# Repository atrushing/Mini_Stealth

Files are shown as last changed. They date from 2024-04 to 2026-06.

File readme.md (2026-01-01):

## Mini Stealth - A Scaled Down Stealthburner

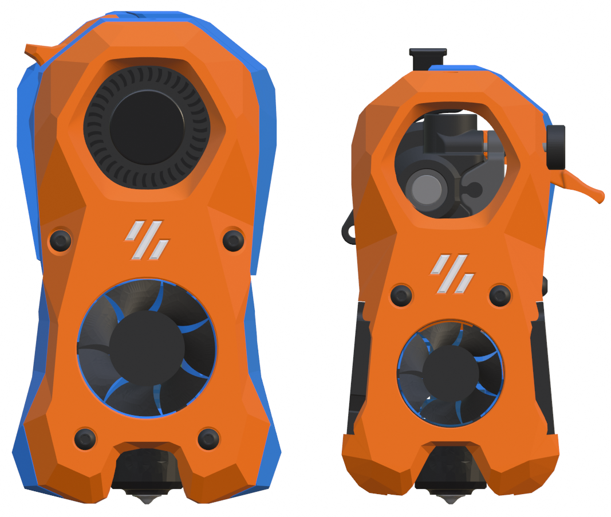
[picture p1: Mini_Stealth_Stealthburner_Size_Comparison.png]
Size Comparison


This is the Version 2 release of the Mini Stealth toolhead. It is about 5/8 the size of the official Stealthburner and weighs considerably less. It uses a pair of 4010 blowers for part cooling and a 3010/2510 fan for the hotend. The blowers use glued in [air guides](https://www.teamfdm.com/forums/topic/1886-vorpal-180-a-printed-printer/?do=findComment&comment=13431&_rid=1756) to increase airflow by [about 20%](https://www.teamfdm.com/forums/topic/1886-vorpal-180-a-printed-printer/?do=findComment&comment=13566&_rid=1756) compared to the Mini Stealth v1. This toolhead was entirely designed in Blender Blender and I only have mesh files available.

The new design mounts the extruder and hotend to a *[core piece](https://www.teamfdm.com/forums/topic/1886-vorpal-180-a-printed-printer/?do=findComment&comment=15428&_rid=1756)* and mounts the blowers, hotend fan and LEDs into the *shroud* that slides onto the core. This makes assembly and maintenance much easier and the extruder can be fully removed while the core remains installed on the printer. There are thirteen extruders supported by the Mini Stealth.

| Orbiter 1.5 | Orbiter 2.0 | Sherpa Mini | LGX Lite | VzHextrudort |
| --- | --- | --- | --- | --- |
| WristWatch BMG | WristWatch G2SA | Sherpa Micro¹ | HGX Lite | Galileo2 SA  |
| Hummingbird | ProtoXtruder <small>(v1&v2)</small> | Creality K1 | | |

¹ <small>There is also a mirrored version of the Sherpa Micro that adds a filament release lever on the left side</small>

There are currently 24 different hotends supported by this toolhead. The cores for the top four in the chart are shared by the others in each group. The bottom ten hotends each have their own cores.

| Slice Mosquito | Phaetus Rapido | Phaetus Dragon ST/HF | T-Labs Dragon ACE |
|:---:|:---:|:---:|:---:|
| Mellow NF Crazy Volcano | Phaetus Rapido UHF | DropEffect neXtG | Goliath |
| Nitram VolcoMosq | Phaetus Dragon UHF | Triangle Labs TZ V6  | |
| | Triangle Labs T-Vocano Dragon | | |
| | Triangle Labs CHCB-V V6DM | | |
| | DropEffect neXtG UHF | | |
| | | | |
| Phaetus Dragonfly BMO | Revo Voron | Bambu Lab X1 |  Creality K1 |
| Phaetus Dragonfly BMS7  | E3D V6 compatible² | Creality Spider Pro  | |
| Phaetus Dragonfly BMS6  | Triangle Labs TCHC TD6S | Dropeffect XG | |

² <small>E3D V6 compatible hotends fit into UHF shrouds and require a clamp secured with 2x M3x10 screws.</small>

Here is an example of how the core and shroud are assembled. There are pockets for 3x6mm magnets. If the magnets aren't seated completly flush, they can prevent the shroud from seating in the correct location.

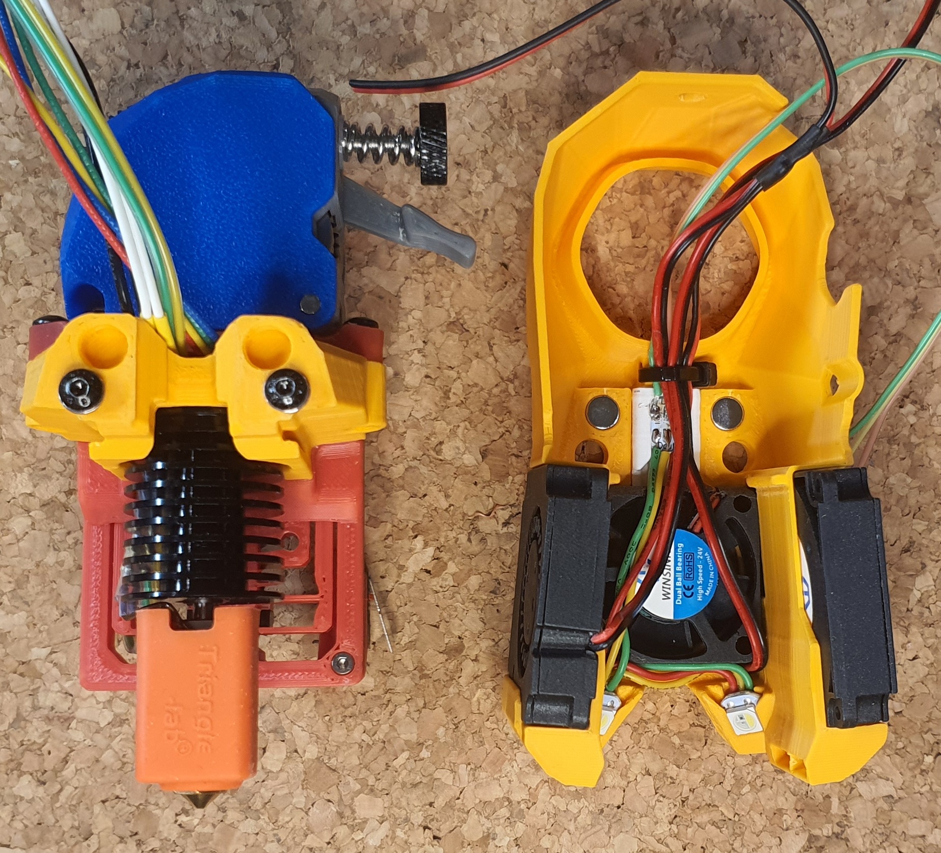
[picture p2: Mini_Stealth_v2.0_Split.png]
Mini Stealth Split


Looking closely you can see three M3 shim washers (DIN988) stacked under each of the M3x40 BHC screws securing the core to the [DAB x-carriage](https://www.teamfdm.com/files/file/760-mini-stealth-dab-beta-release/). Some component combinations will require these shims, such as with the MGN9 mod on a V0.1/2 in order to avoid crushing the linear carriage when installing. It is best practice to do a dry-run and measure clearances before final installation.

The .stl files in the Common_Parts folder should be compatible across the entire range of Mini Stealth versions. This includes all of the x-carriage options (DAB as well) and supplemental parts such as LED mounts and diffuser.

There are 90 different shrouds grouped by extruder type. Each of the 90 shrouds comes in four flavors. The basic shroud, a ZeroClick version and left or right probe-mount versions. The last two use M2.5x6 flathead screws to fit brackets that hold [six different probes](https://raw.githubusercontent.com/atrushing/Mini_Stealth/main/Ender_3_parts/Ender_3_Probe_Options_1.png). There are also versions of all of these shrouds designed to fit a 2510 hotend fan. The Goliath shrouds are only available as CropTop with a 2510 fan. 

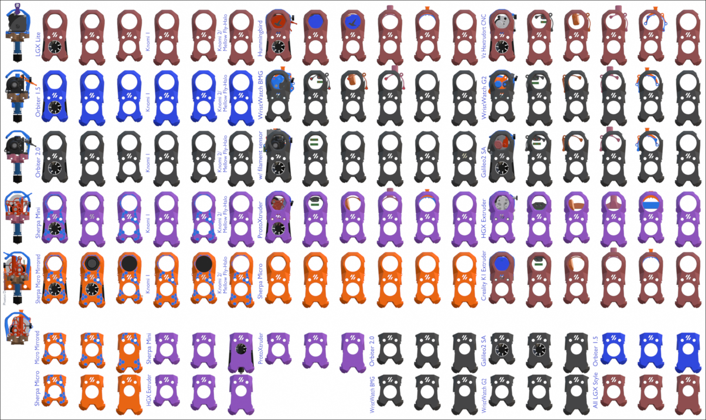
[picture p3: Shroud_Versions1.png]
Shroud Versions1


There are six sets of core pieces with unique mounting holes for different extruder groups. Each extruder folder has a copy of the applicable core pieces to avoid confusion. The extruders in the image above with magenta shrouds all use an adapter plate to secure the extruder to the core piece. 

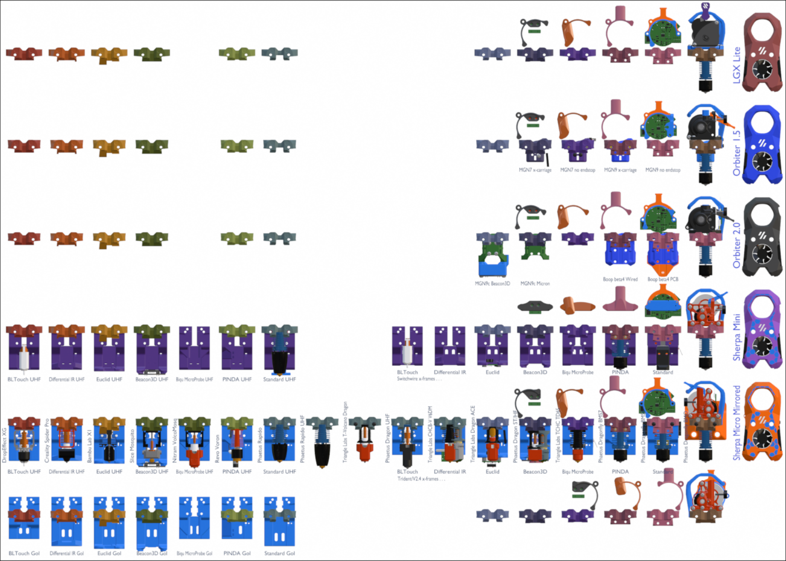
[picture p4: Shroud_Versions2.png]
Shroud Versions2


There are four different motor bridge pieces for each extruder that address different cable management options. The umbilical PCB option uses a pair of heat-set inserts to secure a secondary printed piece. The motor_bridge for the cable chains uses M2.5 flathead screws threaded into the plastic to attach the secondary piece.

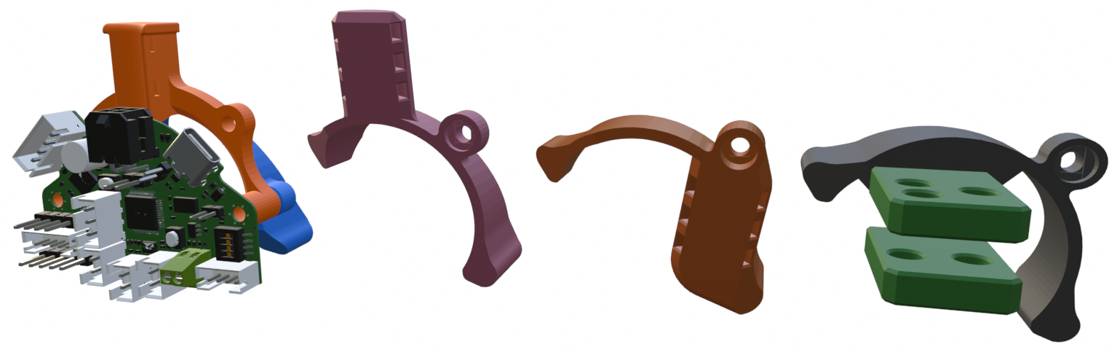
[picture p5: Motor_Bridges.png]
Motor Bridges


### Heatset Inserts

- The only hotends that require heat-set inserts are the Bambu and the Dragonfly BMS models.

- Most of the extruders are secured with two inserts from below the *core* piece but some use M3 square nuts installed from the side of the *core*

- Most of the x-carriages will use a pair of inserts from the back to secure the *core*

- Most of the cable_doors will use one insert on the non-hinged side to secure it to the back side of the *core*

- A few cable_doors use two inserts on either side at the bottom and then hook under the top of the shroud

- The Omron probe (and Klicky) requires a pair of inserts in the retainer_bracket behind the x-frames

- Mounting a Beacon/Cartographer probe uses two inserts in the bottom of the x-frames

- The motor_bridge mounts for 2 or 3 hole cable chains will require inserts

- Mounting an umbilical PCB requires two inserts. Depending on which 
  extruder is used, the second image below shows where they are installed

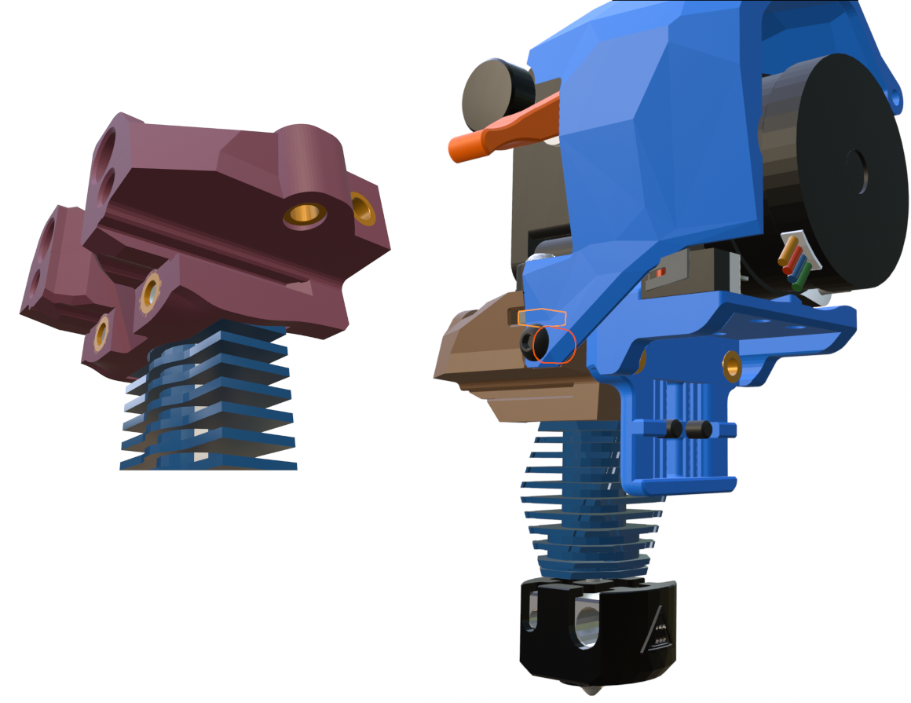
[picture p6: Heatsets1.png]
Heatsets1


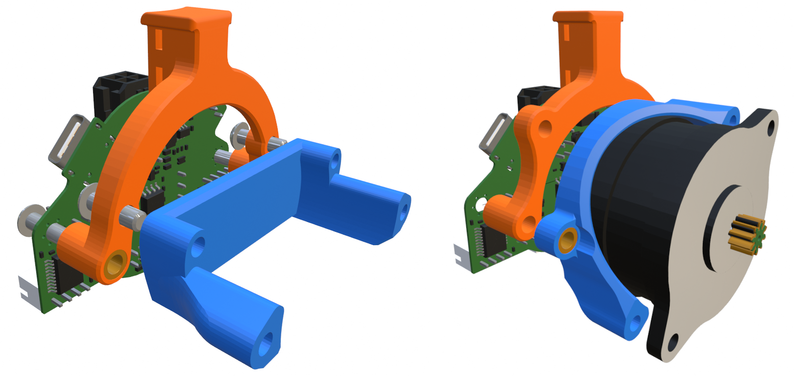
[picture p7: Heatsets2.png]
Heatsets2


### Mini Stealth - Vz Goliath Hotend Versions

This is an effort at making a shroud to fit the Goliath Air hotend. There are only crop-top shrouds available which use 4010 blowers for part cooling and a 2510 radial fan for cooling the hotend heat-break.

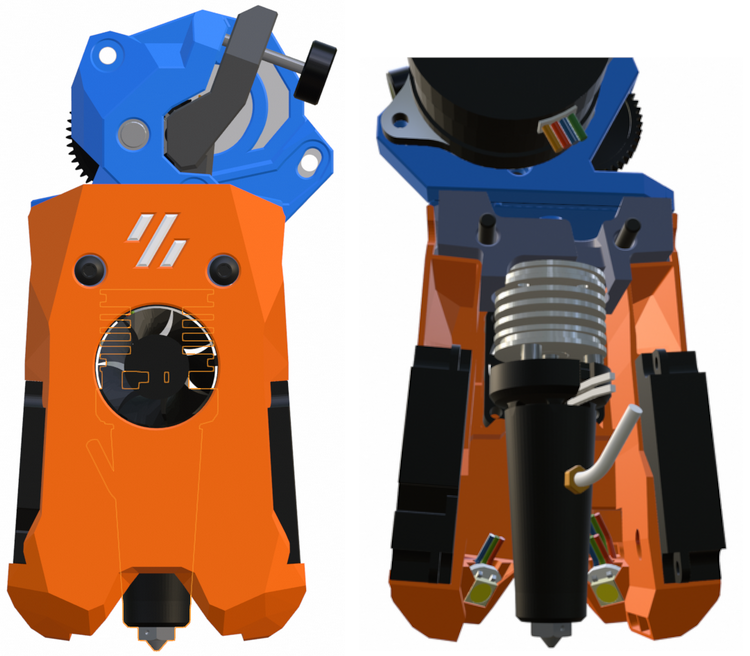
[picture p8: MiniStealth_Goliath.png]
Goliath 01


The Goliath hotend fits onto any of the existing DragonAce core pieces in this repository. As installed, the nozzle sits 18.5mm lower than any of the standard length hotends and 10mm lower than the UHF hotends.

There are spring clips built into the shroud to hold the 2510 fan in place. They are designed with a 0.3mm gap that will not require supports but should allow them to act as springs. These might still need some adjustment.

### Addendum

I still need to work up new assembly instructions for this v2 toolhead. For supporting these designs, I am most active over on [TeamFDM.com](https://www.teamfdm.com/profile/1756-atrushing/content/?type=downloads_file&change_section=1) and will be happy to [answer questions](https://www.teamfdm.com/forums/topic/3433-mini-stealth-v2-is-available) there. The Mini Stealth files available on TeamFDM are of the version 1 release, while the current v2 files are all here.

I started working on a [configurator](https://atrushing.github.io/Sidewinder-Switchwire/) for this toolhead but I still have a lot to learn about JavaScript. If anyone would like to help with this, please drop me a message on [TeamFDM](https://www.teamfdm.com/profile/1756-atrushing/).

If you would like to support the development of these mods I would be very grateful. [](https://paypal.me/atrushing)

### - - Changelog - -

#### 20 Dec 2025

- Added WristWatch Orbiter 2.x extruder and Mini Stealth shrouds for it

#### 19 Dec 2025

- Minor geometry improvement for WW-BMG shrouds

#### 16 Nov 2025 

- Added WW BMG remix with Filament Cutter

#### 26 Oct 2025 

- Added x-carriage to fit the Tiny-M printer

#### 25 Sep 2025 

- Added BTT Eddy side-mount variants

#### 3 Sep 2025 

- Added x-frames for Voron Legacy printers

#### 31 May 2025 

- Merge pull request #6 from darkautism/main
- Add 4040 VSlot support

#### 22 May 2025

- Added new cores for E3D V6 compatible hotends (to fit UHF shrouds)

#### 14 May 2025

- Added rigid x-carriages for MGN12C and MGN12H linear rails

#### 1 May 2025

- Added rigid x-carriages for MGN9C and MGN9H linear rails

#### 24 Apr 2025

- Updated DAB design and readme instructions

#### 6 Apr 2025

- Added StealthChanger backplate and dock in the Common Parts folder

#### 30 Mar 2025

- Modified new core pieces to allow JST connector to fit through wire channel
- Added new style of core pieces for all extruders supported by Mini Stealth

#### 26 Mar 2025

- Added Prusa MK3 x-carriage options

#### 16 Mar 2025

- Added new style of core pieces for the Sherpa Mini mount extruders

#### 6 Feb 2025

- Added support for WristWatch BMG & G2SA extruders

- There are now two versions for the Sherpa Micro, normal and mirrored. (the mirrored version fits my modification with a filament release lever on the left side)

- Added the modded+mirrored Sherpa Micro .stl files in this repo

- Added support for HGX Lite extruder

- Added support for Creality K1 extruder

- Added support for Goliath hotend (CropTop only)

- Added 2.4/Trident x-frames for Goliath hotend

- Minor shroud geometry cleanup

- Fixed mis-aligned first layer of x-frame pieces

- Added support for 2510 hotend fan to all shroud options

- Added right side probe support

- Added new hex patterns to fit the 2510 shrouds

- Re-organized GitHub folder structure based on extruder selection

- Update and improve readme files

#### 6 Apr 2024 v2.0 Release

- More extruders have been added.

- More hotends have been added.

- The shroud is now separate from the core.

- The shroud fits onto the core with a pair of sliding grooves and can fit magnets to improve the connection as needed.

- The hotend can be installed to the core and then mounted to the printers' gantry.

- Everything else can be installed (or removed) while on the printer.

- All core pieces and shrouds are compatible with 25mm or 26mm x-carriages. :: i.e. Mini Stealthburner CNC aluminum carriages.

- All x-carriages are compatible with any hotend/extruder combination.

- There are specific UHF x-frames for Trident, V2.4 and Switchwire printers to provide probe compatibility.

- The V0.1/V0.2 x-carriages are much stiffer with side ribs that require included XY_Joint_Upper pieces.

- The 25mm spacing improves the Ender 3 mount which is available in the repo.

- The LED diffuser and carriage are new and simplified.

- The Rainbow BARF carriage is now in two part and should be easier to fit.

- All shrouds have standard, ZeroClick and Differential IR options.

- The 4010 blowers use a glued in (CA glue) air guide to increase airflow at the nozzle.

- The UHF shrouds have been re-worked to put the 4010 blowers lower, matching the standard shrouds.

- New probe mounting side brackets have been added that fit the Differential IR shrouds. Thanks to @Titus A Duxass for the concept!
  
  - Biqu MicroProbe
  
  - PINDA
  
  - BL-Touch

- I have added Knomi2 shrouds that should also fit the Mellow Fly-Halo display.

- I have made Crop-Top shrouds for each extruder option.

- Each extruder has motor_bridge pieces that support cable management, cable chain mounts or umbilical PCB mounting.

- The umbilical PCB mounts are vertical for better ADXL readings.

- All parts have been modified for cleaner and more consistent geometry across versions.

#### 16 May 2023 v1.2.5

- Added Euclid and Biqu MicroProbe mounts for Trident, 2.4 and Switchwire

- Upload corrected version of ZeroClick Mount

#### 12 Apr 2023 v1.2.5

- Added missing Crop-Top .stl and image

#### 4 Mar 2023 v1.2.5

- Added feature to x-frame_right to allow mounting X limit switch as with the Umbilical Mod

- Added Beacon3D compatible x-frame sets for V2.4, Trident and for Switchwire

- Added new shrouds to fit the Creality Spider Pro hotend

#### 28 Feb 2023 v1.2.4

- Added wire slot for LEDs wires to fit past 3010 fan. The last revision wasn't sufficient.

- All shroud files are new.

#### 26 Feb 2023 v1.2.3

- Fixed pinching of LED wires when using 3010 fan.

#### 24 Feb 2023 v1.2.2

- Improved rigidity of x-carriage mounting for the V0.1/V0.2 by moving the heat-set insert to the back side.

- This requires 5mm longer screws to mount the shroud.

- Improved how the front two screws fit into the shroud when mounting onto the carriage. This used to be chamfered but now is flat for better load transfer. All shroud .stl files are new.

- Uploaded new version of x-frame pieces with more clearance to fit 4010 blowers from different suppliers.

- Added x-frame pieces for Switchwire builds. These pieces can fit the standard capacitive probe or fit a BL-Touch. Since the stepper sits very low with the Orbiter, the Z height of the nozzle is raised by 3mm compared to the official Switchwire x-frame design.

#### 22 Feb 2023 v1.2.1

- Added a hex pattern and tutorial based on the 3DP-MAMSIH mod

#### 13 Feb 2023 v1.2.0

- Improved cooling by aiming ducts 6 deg lower at hotend nozzle tip.

- Added compatibility with 3010 hotend fan. 3007 fan still fits using clip-in adapter

- Added versions for ZeroClick mod

- Added versions for differential IR probe.

- Added newer version for the VolcoMosq hotend

- Minor geometry cleanup.

- All shroud .stl files are new

#### 10 Feb 2023

- Release of Sherpa Mini version

#### 31 Jan 2023 v1.1.7

- Added stretched versions for the Rapido UHF, Dragon UHF and the VolcoMosq hotends

#### 19 Jan 2023 v1.1.6

- Added Umbilical-mod mount remixed from skuep's mod

- Replaced motor_bridge with version with space for M3 heat set inserts to allow for mounting PCB or Umbilical-mod behind the stepper

#### 22 Nov 2022 v1.1.5

- Added versions for Slice Mosquito hotend

#### 10 Nov 2022 v1.1.4

- Added an x_carriage for the V0.1 MGN-9 mod

#### 1 Nov 2022

- Release of LGX Lite version

#### 24 Oct 2022 v1.1.3

- Added versions to fit the Rapido HF hotend

#### 22 Oct 2022 v1.1.2

- Added versions to fit the Revo Voron hotend

#### 22 Oct 2022 v1.1.1

- Fixed mesh error in [a]_MIni_Stlb_Orbiter_2.0_main_body.stl

#### 17 Oct 2022 v1.1.0

- Fixed wire clearance issue on x_carriage_mini_stlb

- Updated all main_body files with with more room for cable routing

#### 15 Oct 2022 v1.0.1

- Added versions for compatibility with the Dragon hotend

- Changed naming scheme for better description of versions

#### 14 Oct 2022 v1.0.0

- Modified 'cable_door' due to interference with V0.1 x-axis endstop.

#### 13 Oct 2022

- Release of Orbiter 2.0 version

#### 30 Sept 2022

- Initial Mini Stealth release (Orbiter 1.5 version)

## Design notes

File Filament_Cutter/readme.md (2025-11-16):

### Wrist Watch BMG with Side Mounted Filament Cutter

This is a remix of the [WW BMG](https://github.com/bythorsthunder/Voron_Mods/tree/main/Wristwatch_Extruder_BMG) extruder which adds a filament cutter below the hobbed gears. It fits replacement Bambu blades and uses a spring from a clicker pen (5mm x 20mm) to keep the blade clear of the filament path until actuated.

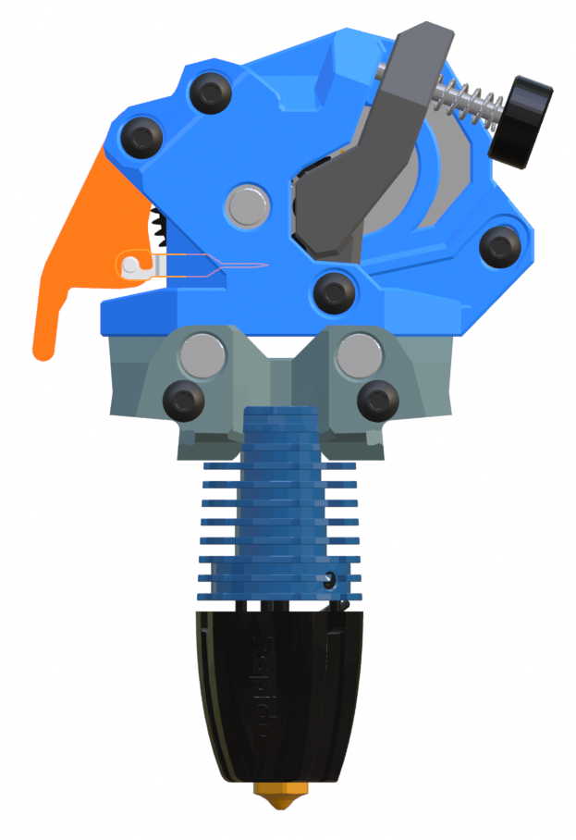
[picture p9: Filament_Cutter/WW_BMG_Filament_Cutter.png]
WW BMG FC


This remix doesn't change any of the functional geometry of the extruder. The cutter arm does require organic supports for the small hook feature that helps grabbing the blade. It uses up to an M3x20 screw for the pivot of the cutter arm. The blade recess in the extruder body might need a little cleanup to ensure that the blade can slide smoothly.

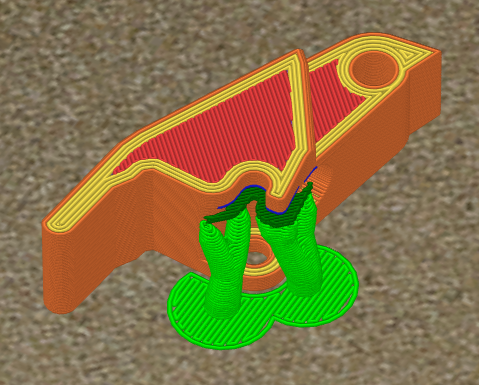
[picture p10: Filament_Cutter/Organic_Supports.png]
Tree Supports


There is an additional subtraction part that removes the necessary material from the Mini Stealth shroud to allow the cutter arm to fit. It has two locating cylinders to align the .stl with the shroud in the slicer. It is easiest to align the parts from the bottom view.

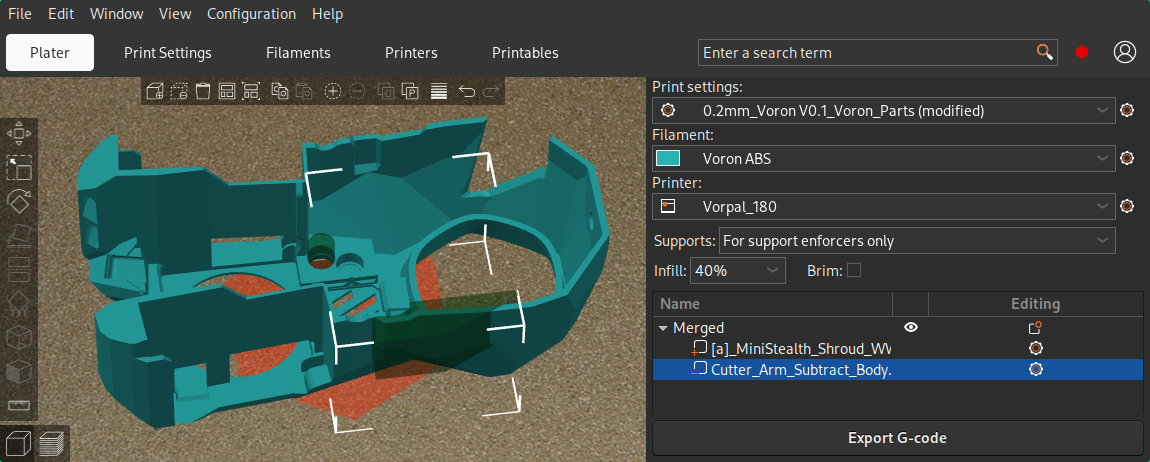
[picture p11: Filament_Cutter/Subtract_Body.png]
Subtract Body


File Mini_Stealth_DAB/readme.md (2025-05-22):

## Mini Stealth DAB

This is a flexure based nozzle probing option for mounting the Mini Stealth toolhead in a Voron Trident or V2.4. It uses a simple linear compliant mechanism to provide ~0.5mm of Z travel while being quite rigid in the other axes. It weighs around 20g fully assembled with Z and X endstops. It should require the same Print_Start preparations as the Voron TAP to ensure a clean nozzle and accurate probing. While probing with a scale on top of the bed, it applys about 600g of force.

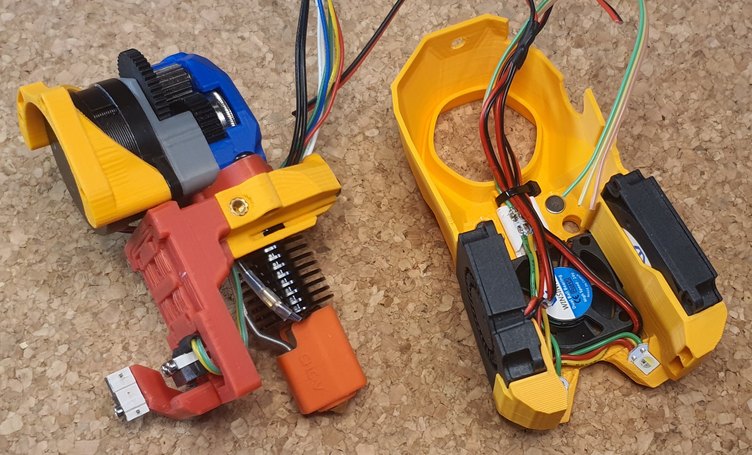
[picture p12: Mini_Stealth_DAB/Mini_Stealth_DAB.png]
Mini Stealth DAB


The new version of the DAB has been adapted to work with my new rigid core pieces. This combination is more reliable than before. While probing, the old version would flex back before lifting the toolhead. It now creates a box structure centered on the linear carriage which restrains the movement better along the Z axis.

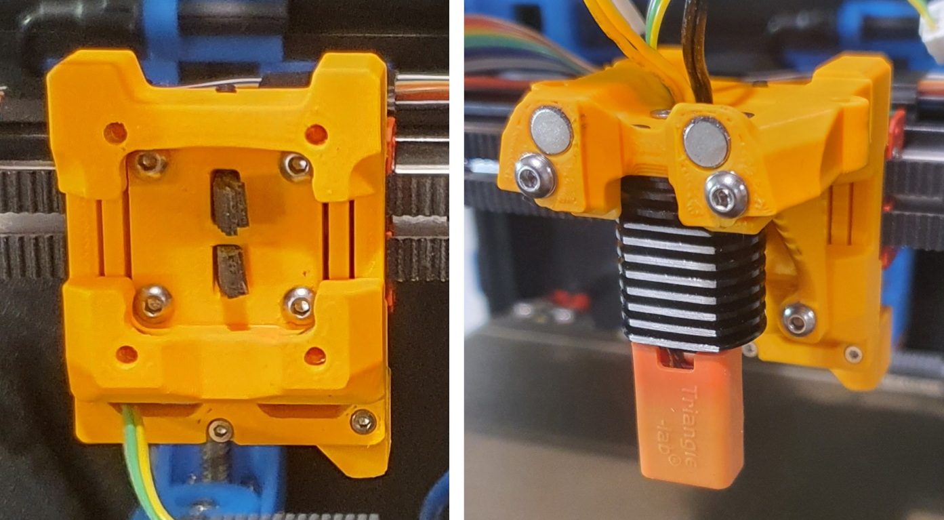
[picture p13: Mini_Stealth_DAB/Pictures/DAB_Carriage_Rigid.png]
Rigid DAB


There are a few supports (shown in green) built in to make printing more reliable. After printing, the two inner sections will need to be gently, but firmly, pried apart from the two bridge sections while being careful not to plastically deform the flexures. There are four pockets for M3 square nuts to secure the Mini Stealth core piece using two M3x45 BHCS at the top and two M3x12 BHCS on the bottom.

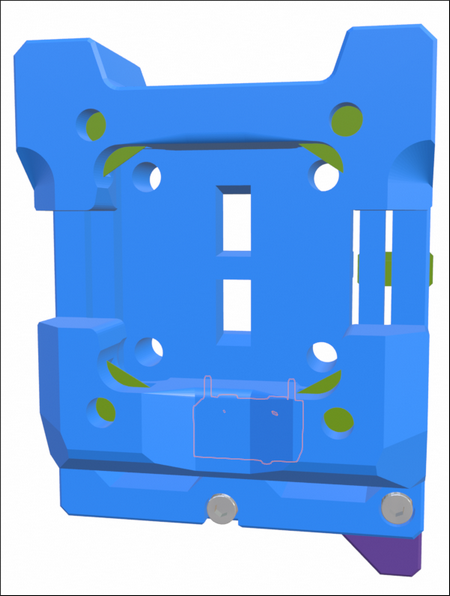
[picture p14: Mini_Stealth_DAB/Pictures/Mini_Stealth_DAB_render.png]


There are several different rear boss pieces depending on where you have your X endstop mounted. This piece is secured with a pair of M2x10 self tapping screws.

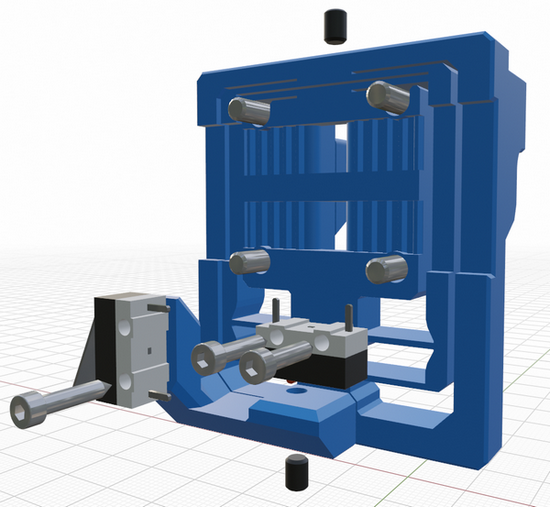
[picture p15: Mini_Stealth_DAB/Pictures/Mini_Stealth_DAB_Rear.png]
Rear View


The flexure works as shown below. The blue center section is fixed to the MGN12H linear carriage. The magenta vertical bars are the intermediate phase and the purple outside frame is the final phase of the flexure. The red bars are the actual flexing parts and are 0.8mm thick.

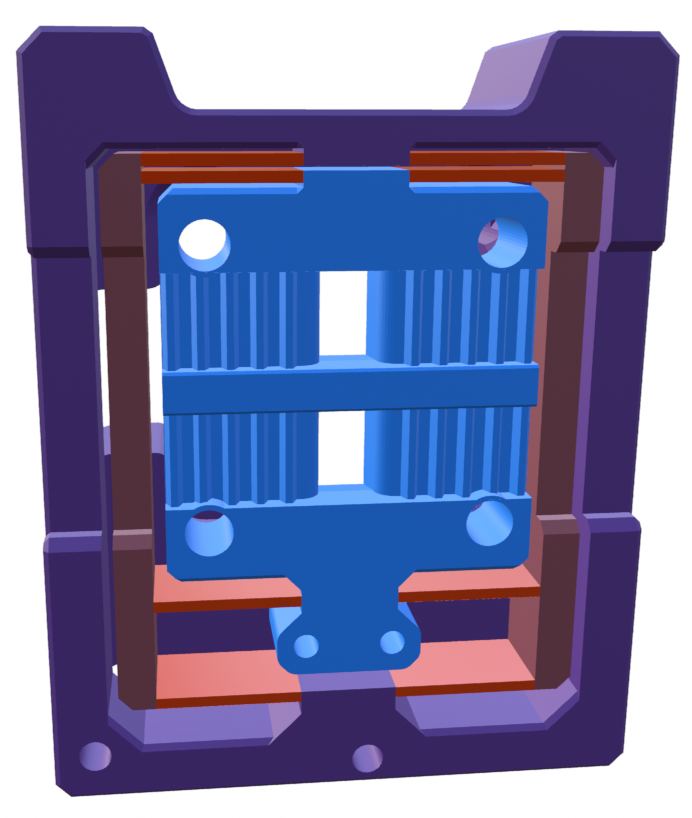
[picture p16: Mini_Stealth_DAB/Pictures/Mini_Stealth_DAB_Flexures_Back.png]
Flexure


### Assembly

- After ensuring that the flexure moves freely, install one of the grub 
  screws in the top and screw it in just enough to remove the reverse Z travel in
   the flexure. This provides a known lower limit of travel.

- Install the Z_Stop_Boss with two M2 x 10 screws from the front.

- Install the Z micro-switch with the red trigger on the left 
  (viewed from the back). The wires can be fed to the front through the 
  lower gap in the flexure.

- Install the other M3 grub screw on the bottom of the DAB_Z_Boss. Screw
   it in until you hear the micro-switch trigger, then slowly turn it back out
   until the trigger releases. This makes the trigger travel distance less
   than 0.5mm.

- Mount the x-carriage to the MGN12C carriage with four M3x12 BHCS. 
  There is room to pull the four belt ends through and trim them at the 
  front face of the DAB.

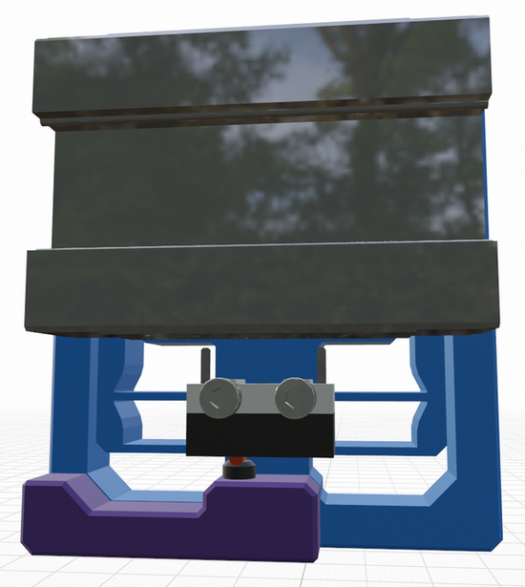
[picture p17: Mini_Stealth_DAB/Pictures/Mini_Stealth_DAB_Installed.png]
DAB Assembled


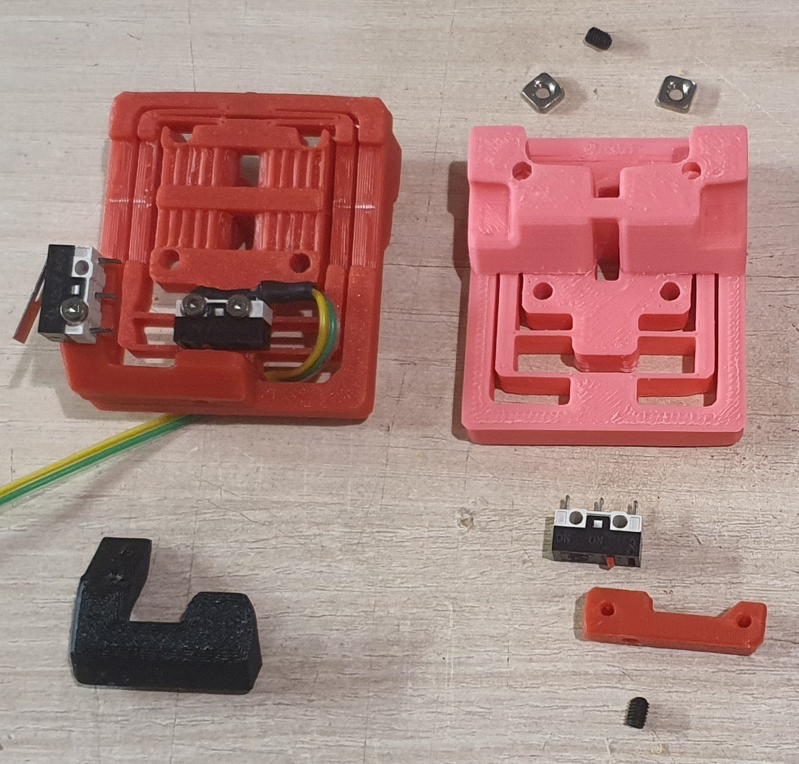
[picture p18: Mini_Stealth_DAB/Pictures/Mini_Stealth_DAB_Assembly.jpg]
Assembled DAB


### Stealthburner Version

This version of DAB is a drop-in replacement for the Stealthburner x-frame pieces. It uses slightly different hardware than the official Stealthburner assembly, as shown in the picture below.

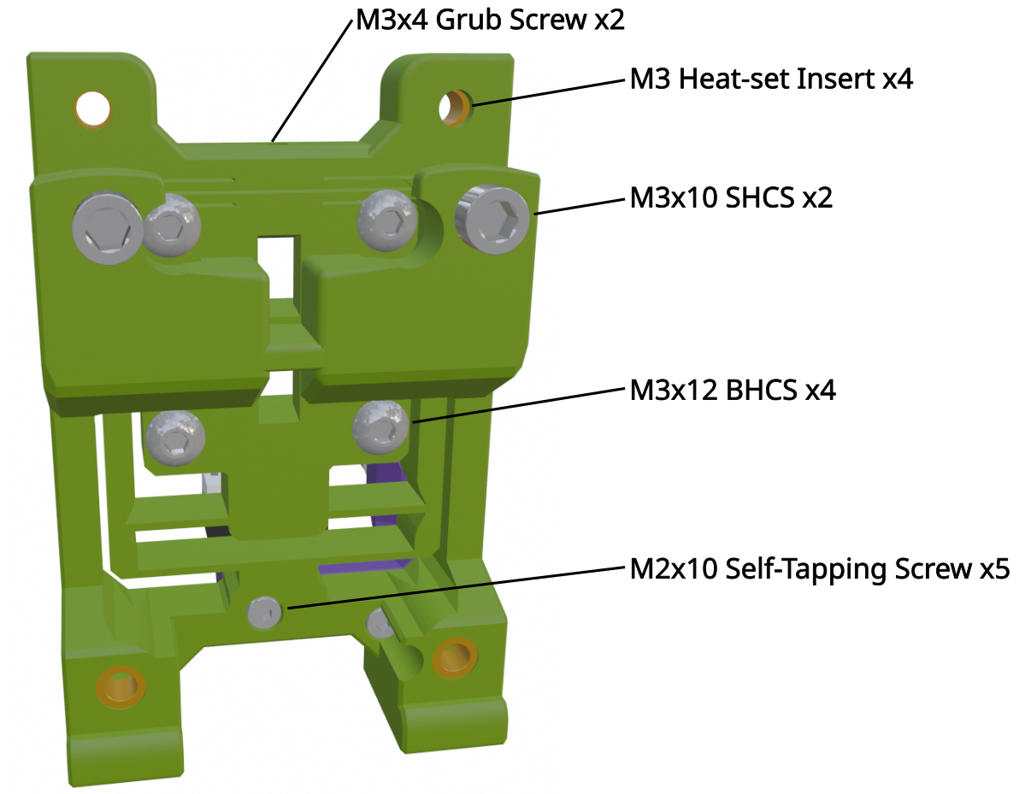
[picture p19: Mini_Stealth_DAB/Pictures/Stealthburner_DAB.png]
Stealthburner DAB


### Stealthburner on a Switchwire

This version of DAB fits a Stealthburner onto a Switchwire. It is printed in two parts and assembled with three M2x10 self tapping screws.

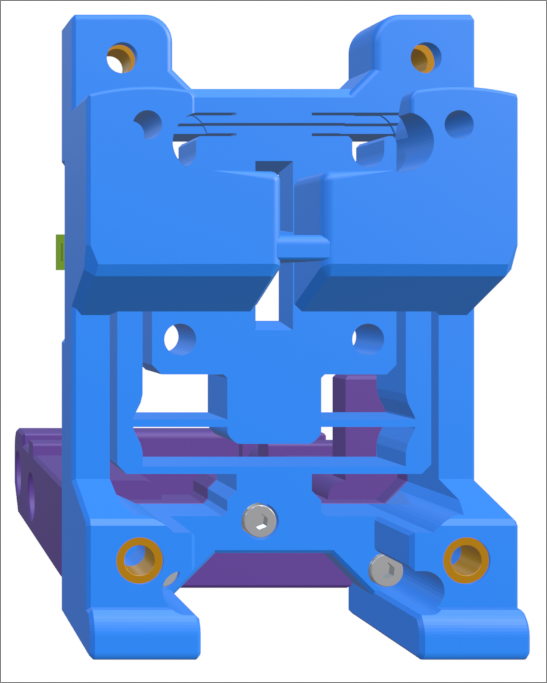
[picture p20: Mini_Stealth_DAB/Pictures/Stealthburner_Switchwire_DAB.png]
Switchwire Stealthburner
 

This is still in Beta and I would appreciate any feedback. I am active on [TeamFDM.com](https://www.teamfdm.com/files/file/760-mini-stealth-dab-beta-release/) and will also keep an eye on any issues posted here.

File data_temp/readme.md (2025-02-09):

This folder holds working files for developing a configurator for the Mini Stealth toolhead.

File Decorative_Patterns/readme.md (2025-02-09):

## Hex Patterns Based on Design by [3DP-MAMSIH](https://www.printables.com/model/225153-voron-stealthburner-face)

Here is a sample of the different versions of the hex-pattern inlay for the Mini Stealth.
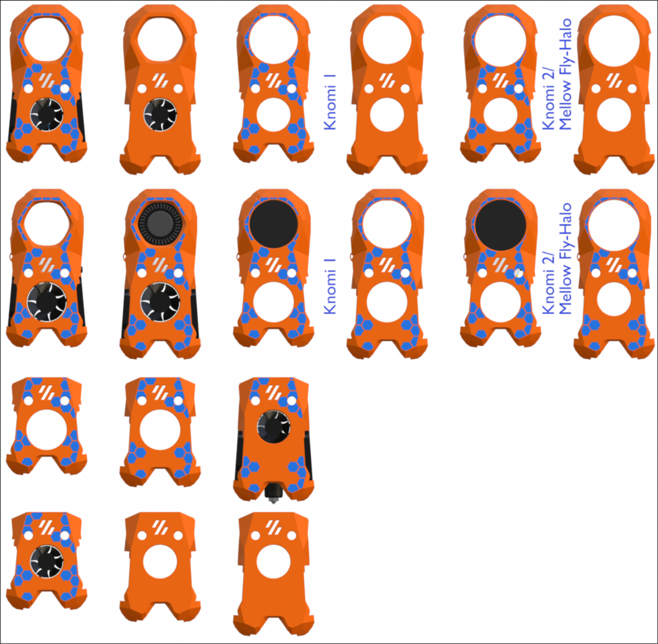
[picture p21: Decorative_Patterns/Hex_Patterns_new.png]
Six Pattern Versions

I wrote a [tutorial](https://www.teamfdm.com/files/tutorials/2-adding-decorative-inlay-negative-body/) on how to apply this pattern within Prusa Slicer. It is also possible to apply the pattern as a multi-color print in Bambu Studio by following the process explained in [this video](https://www.youtube.com/watch?v=UekEbg_ZkgI).

There are now hex-pattern .stls for Crop Top shrouds (standard, UHF and Goliath).

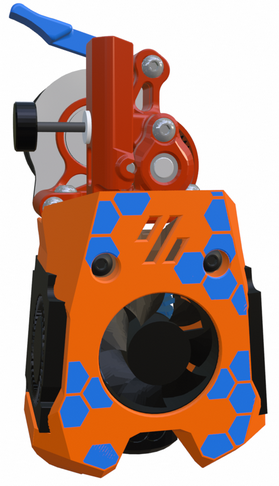
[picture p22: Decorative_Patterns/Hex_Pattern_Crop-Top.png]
Crop Hex


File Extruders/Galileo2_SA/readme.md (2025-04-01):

## Mini Stealth - [Galileo2 SA](https://github.com/JaredC01/Galileo2/tree/main/galileo2_standalone)

This version of the Mini Stealth is modified from the Orbiter 2.0 version.

The Galileo2 StandAlone extruder requires a modified idler arm to fit cleanly inside of the Mini Stealth unless using a Crop-Top version. Their filament advance thumb screw will also collide with a non Crop-Top Mini Stealth.

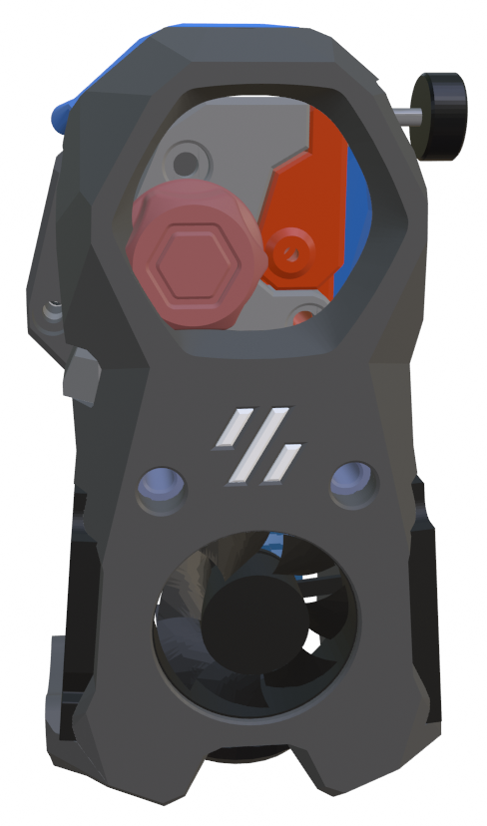
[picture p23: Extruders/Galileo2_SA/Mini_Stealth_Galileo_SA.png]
Mini Stealth Galileo SA


For more information, questions and feedback, I am most active at [TeamFDM.com](https://www.teamfdm.com/files/file/612-mini-stealth-orbiter-20/?tab=comments) but the files here are the most current.

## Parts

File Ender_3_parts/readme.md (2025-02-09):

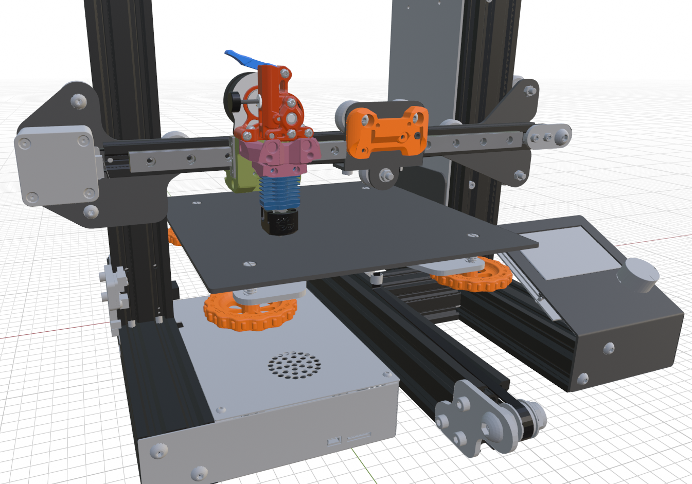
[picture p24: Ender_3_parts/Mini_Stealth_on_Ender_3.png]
Ender 3


## Ender 3 Installation Options

Here are centered mounts for installing the Mini Stealth (UHF or Standard) on an Ender 3. 

Ender 3 Mount

For some extruder options, the stepper motor sits rather low and might require some modification of the V-wheel plate.

Ender 3 Stepper Clearance

I have also made side mounts for several probes that can be installed on the ProbeLeft/Right shroud versions. They require M2.5x6 flathead screws to connect the brackets to the shroud while leaving clearance for the 4010 blower.

There are additional Switchwire style mounts for front or top mounted linear rails. The front mounted MGN12 rail can be installed directly on the 2020 extrusion. The rest of the linear rail mod variations are designed assuming 4.5mm of spacing between the 2020 extrusion and the back of the linear rail. The timing belt is secured from below with a toothed wedge. Further information is available in the TeamFDM comments starting [here](https://www.teamfdm.com/files/file/657-mini-stealth-mini-sherpa/?do=findComment&comment=1920&_rid=1756) but the GitHub files are more current.

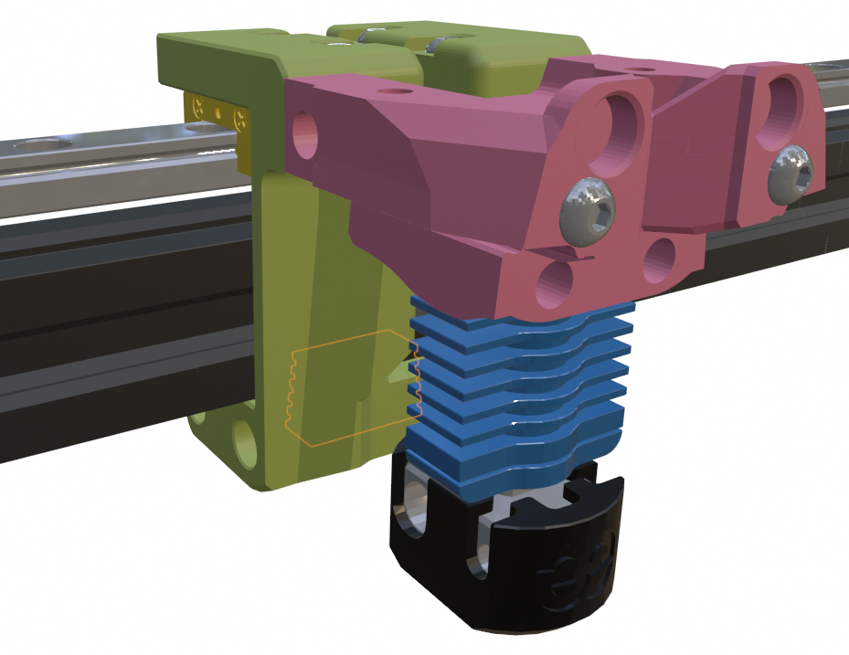
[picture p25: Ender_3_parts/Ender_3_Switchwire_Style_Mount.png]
Switchwire Style Mount

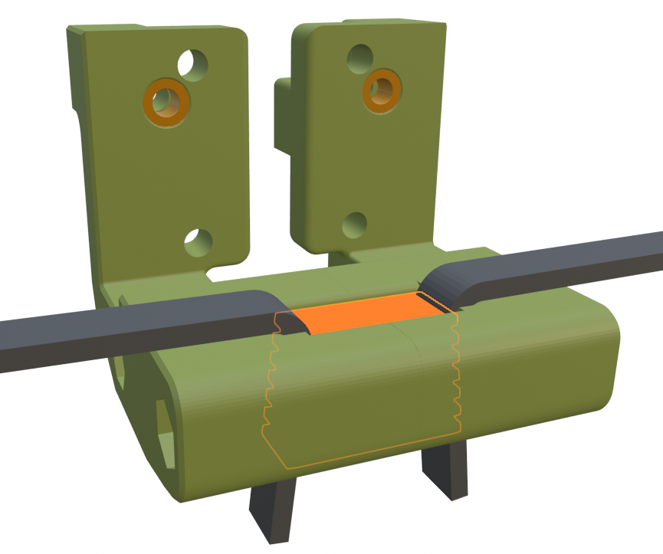
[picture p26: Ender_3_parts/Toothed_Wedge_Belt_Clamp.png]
Toothed Wedge


With the front-mounted linear rails, there is room to install a Beacon3D probe or a Biqu MicroProbe under the x-carriage. The MicroProbe is secured with M2x10 self-tapping screws.

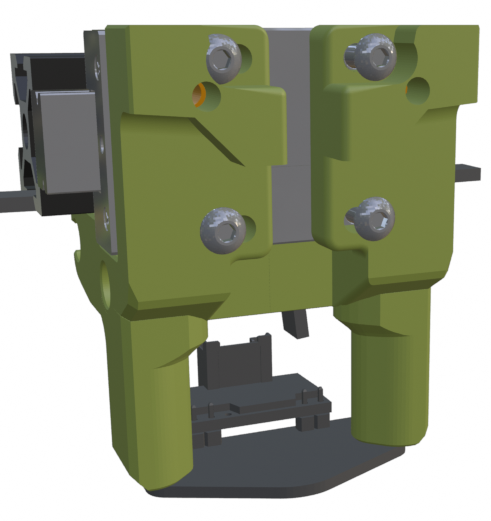
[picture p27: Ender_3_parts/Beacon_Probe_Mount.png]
Beacon Probe Mount

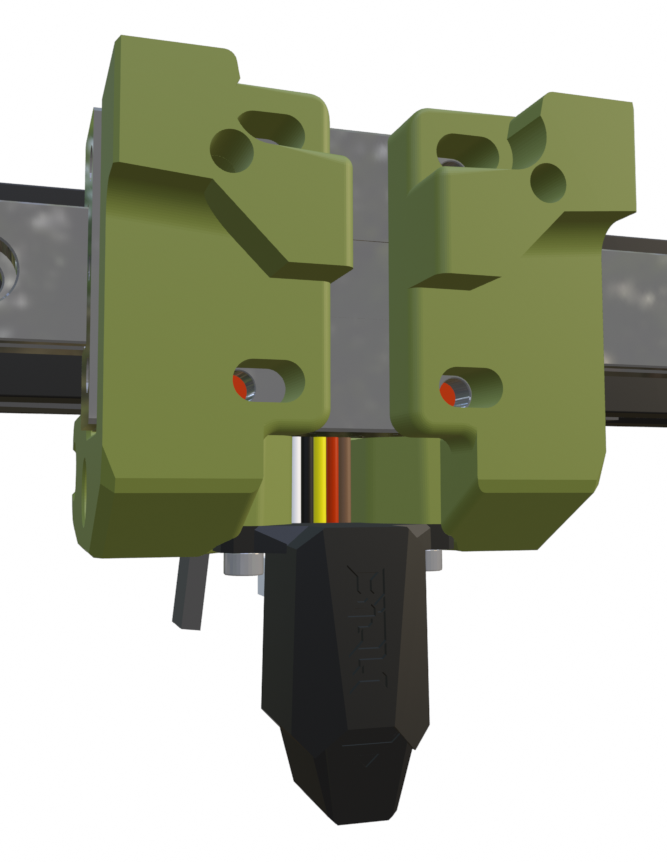
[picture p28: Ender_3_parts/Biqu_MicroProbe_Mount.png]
Biqu MicroProbe Mount


## Ender 6 Installation

The Ender 6 mount has been improved and should fit most of the extruder options except the Orbiter 1.5 and Galileo SA.

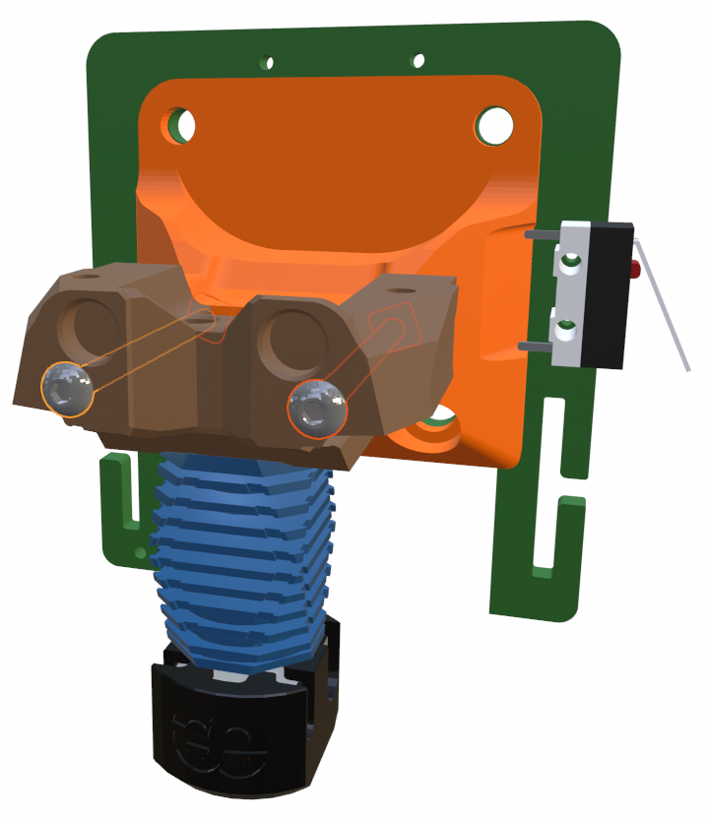
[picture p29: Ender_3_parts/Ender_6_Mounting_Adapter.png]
Ender 6 Mount


## Side-Mount Probe Offsets

| | BL-Touch | CR-Touch | PINDA | Diff IR | MicroProbe | BTT Eddy |
| --- | --- | --- | ----- | --- | --- | --- |
| X Offset | 37.5 mm  | 40 mm | 37 mm | 32 mm | 38 mm | 42 mm |
| Y Offset | -6 mm | -6 mm | -6 mm | -4 mm | -6 mm | -6 mm |

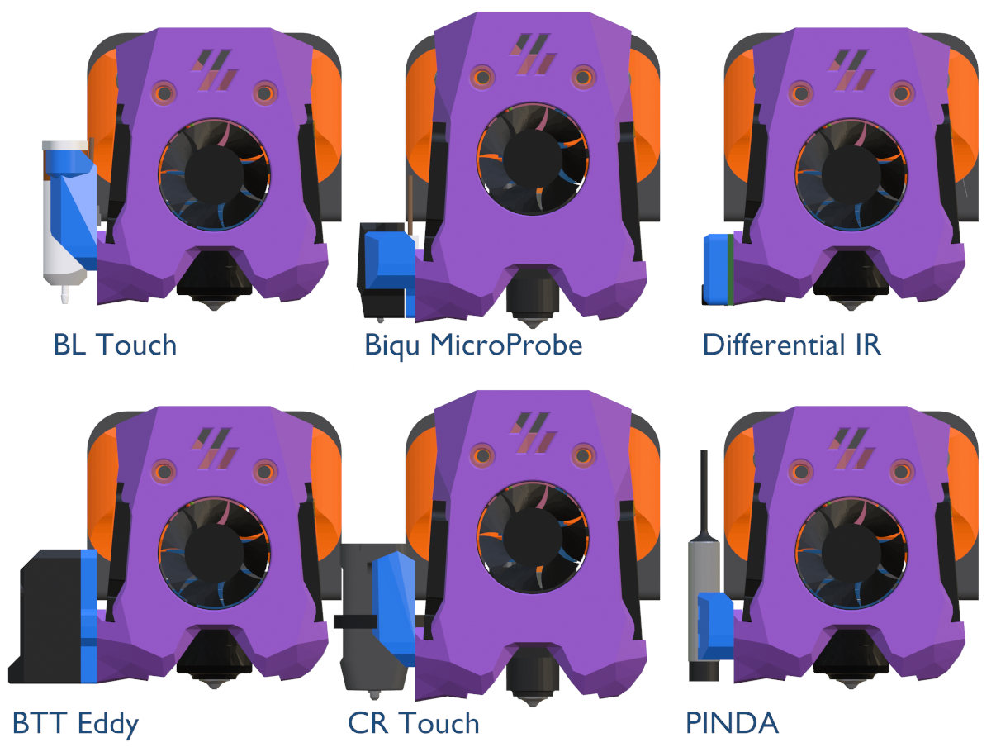
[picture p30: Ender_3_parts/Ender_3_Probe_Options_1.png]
Ender 3 Probes 1


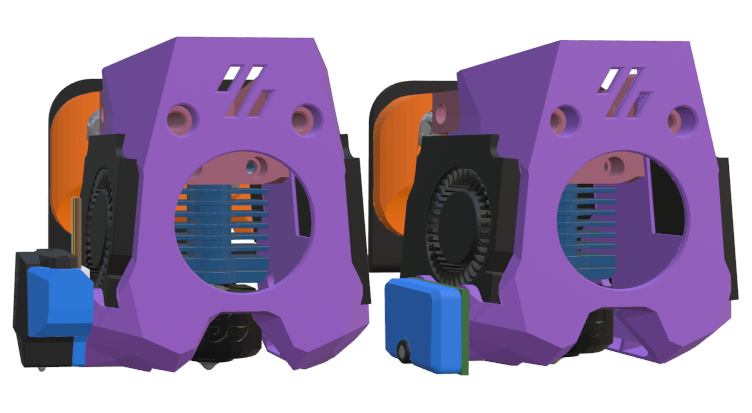
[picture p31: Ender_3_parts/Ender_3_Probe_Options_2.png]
Ender 3 Probes 2


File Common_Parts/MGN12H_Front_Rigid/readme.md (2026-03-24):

## MGN12H Front Mounted Rigid X-Carriages

Front View

This is a set of x-carriages for the Mini Stealth designed to fit on a front facing MGN12H linear rail. They mate with the new rigid core pieces that are available in their respective extruder folders. These x-carriages raise the toolhead by around 8mm causing some of the probes to not fit below the 2020 X extrusion. The image below shows which probes fit with the Goliath hotend, the UHF hotends and all standard hotends.

Overview

The belt management geometry is borrowed from the [Boop beta 4](https://github.com/PrintersForAnts/Boop) carriage by PrintersForAnts and uses two of their belt clamps secured with M3x6 BHCS and M3 hex nuts. 

A couple of the probes require an additional probe mount piece (shown in brown above). These are secured with a pair of M2x10 self tapping screws.

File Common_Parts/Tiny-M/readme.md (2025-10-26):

## Tiny-M x-carriage - Mini Stealth

Tiny-M x-carriage

This x-carriage fits the newer rigid core pieces and uses a pair of M3x45 and a pair of M3x10 BHCS to mount the core onto the x-carriage. Due to space constraints, the top two screws use square nuts inserted from the sides and the lower two screws use heat-set inserts installed from behind.

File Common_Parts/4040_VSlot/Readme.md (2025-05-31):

# 4040 V-Slot support

Only supports the UHF hotend due to the extended length of the 4040 aluminum Z-axis.

Using this carriage on the CP-01 results in a loss of 20mm of X-axis travel.

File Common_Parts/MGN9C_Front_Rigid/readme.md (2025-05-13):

## MGN9C Front Mounted Rigid X-Carriages

Front View

This is a set of x-carriages for the Mini Stealth designed to fit on a front facing MGN9C linear rail. They mate with the new rigid core pieces that are available in their respective extruder folders. These x-carriages raise the toolhead by around 8mm causing some of the probes to not fit below the 2020 X extrusion. The image below shows which probes fit with the Goliath hotend, the UHF hotends and all standard hotends.

Overview

The belt management geometry is borrowed from the [Boop beta 4](https://github.com/PrintersForAnts/Boop) carriage by PrintersForAnts and uses two of their belt clamps secured with M3x6 BHCS and M3 hex nuts. 

A couple of the probes require an additional probe mount piece (shown in brown above). These are secured with a pair of M2x10 self tapping screws.

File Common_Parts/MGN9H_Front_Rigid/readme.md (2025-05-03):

## MGN9H Front Mounted Rigid X-Carriages

Front View

This is a set of x-carriages for the Mini Stealth designed to fit on a front facing MGN9H linear rail. They mate with the new rigid core pieces that are available in their respective extruder folders. These x-carriages raise the toolhead by around 8mm causing some of the probes to not fit below the 2020 X extrusion. The image below shows which probes fit with the Goliath hotend, the UHF hotends and all standard hotends.

Overview

The belt management geometry is borrowed from the [Boop beta 4](https://github.com/PrintersForAnts/Boop) carriage by PrintersForAnts and uses two of their belt clamps secured with M3x6 BHCS and M3 hex nuts. 

A couple of the probes require an additional probe mount piece (shown in brown above). These are secured with a pair of M2x10 self tapping screws.

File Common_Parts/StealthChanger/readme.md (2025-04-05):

## StealthChanger Backplate

StealthChanger Backplate

This is my first take at designing a StealthChanger backplate for mounting the Mini Stealth toolhead. I started with the Dragon Burner backplate and took a few creative liberties with the geometry. This design works in conjuction with my new, more rigid, core pieces so that no extra spacer piece is needed.

This setup should fit the following extruders although some of them are quite tight:

- Sherpa Mini

- Sherpa Micro

- Galileo 2 SA

- WristWatch BMG

- WristWatch G2

- Vz Hextrudort CNC

- LGX Lite

- Hummingbird

- Creality K1

It uses a pair of M3x45 BHCS and a pair of M3x10 BHCS to mount the core to the backplate.

This design should fit any of the hotends supported by the Mini Stealth including the UHF variants as well as the Goliath.

There is also a .blend file that is a complete assembly of the ModularDock, shuttle, backplate and toolhead. This is meant for reference and its geometry may not be up to date with the .stl files.

I will try to modify some of my motor-bridge pieces to see if I can get the umbilical PCB mounts to fit better for the extruders that have very low seating stepper motors.

Please leave feedback, positive or negative, here as an issue or over on [TeamFDM.com](https://www.teamfdm.com/forums/topic/3433-mini-stealth-v2-is-available/).

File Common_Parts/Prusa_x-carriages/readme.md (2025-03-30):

## Prusa X-Carriage

Prusa1

I have designed a backplate that allows the Mini Stealth to be installed onto a Prusa MK3 series printer. It might fit the MK4 as well but I cannot validate this.

This setup should fit most all of the hotends supported by the Mini Stealth. The extruders with low seating stepper motors will have collision issues with the upper LM8UU bearings. The following extruders should be viable options but may still be a tight fit:

- Sherpa Mini

- Sherpa Micro

- Galileo 2 SA

- WristWatch BMG

- WristWatch G2

- Vz Hextrudort CNC

- LGX Lite

- Hummingbird

- Creality K1

It uses a new, more rigid, set of core pieces that I have recently developed. I kept the Prusa geometry and assembly as similar to standard as possible but this design does require eight M3x4x5 heat-set inserts; four to assemble the x-carriage and four to mount the Mini Stealth. It still uses one M3 square nut and an M3 hex nut to secure the stock Prusa cable-holder.

Heat-Set Inserts 1

Heat-Set Inserts 2

Assembled Rear View

### Hardware

- 8x M3x4x5 Heat-set inserts (Voron Standard)

- 2x M3x45 BHCS - secure core piece to x-carriage

- 2x M3x14 BHCS - secure core piece to x-carriage

- 1x M3x40 BHCS - secure Prusa cable-holder

- 1x M3 Hex nut - secure Prusa cable-holder

- 4x M3x20 BHCS - assemble front and back x-carriage pieces

- 1x M3x10 BHCS - assemble front and back x-carriage pieces

- 1x M3 Square nut - assemble front and back x-carriage pieces

- 2x Zip-ties - secure front x-carriage piece to top LM8UU bearings

- 6x Zip-ties - bottom cable routing along cable-holder

- 2x Zip-ties - secure side mounted PINDA probe

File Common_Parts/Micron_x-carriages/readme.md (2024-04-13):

## PrintersForAnts - X Carriage Options

These Boop_front pieces (shown in blue below) replace the *front* and *upper* pieces from the P4A beta4 design. You will still need the *boop_center* piece (orange) and *belt_clamps* from the official [beta4 GitHub](https://github.com/PrintersForAnts/Boop/tree/main/beta_4/STL) page.

Boop beta4 Front

The mgn9c_toolhead_carriage pieces here are slightly remixed from the [Micron MiniAB](https://github.com/PrintersForAnts/Micron/blob/main/STLs/Gantry/Toolhead/MiniAB/mgn9c_toolhead_carriage.stl) carriage in order to make clearance for the different extruders supported by the Mini Stealth v2. To mount a Beacon probe you will need the *carriage_Beacon3D* as well as my custom *probe_mount_beacon*.

All of these x-carriage options should fit any extruder supported by the Mini Stealth.

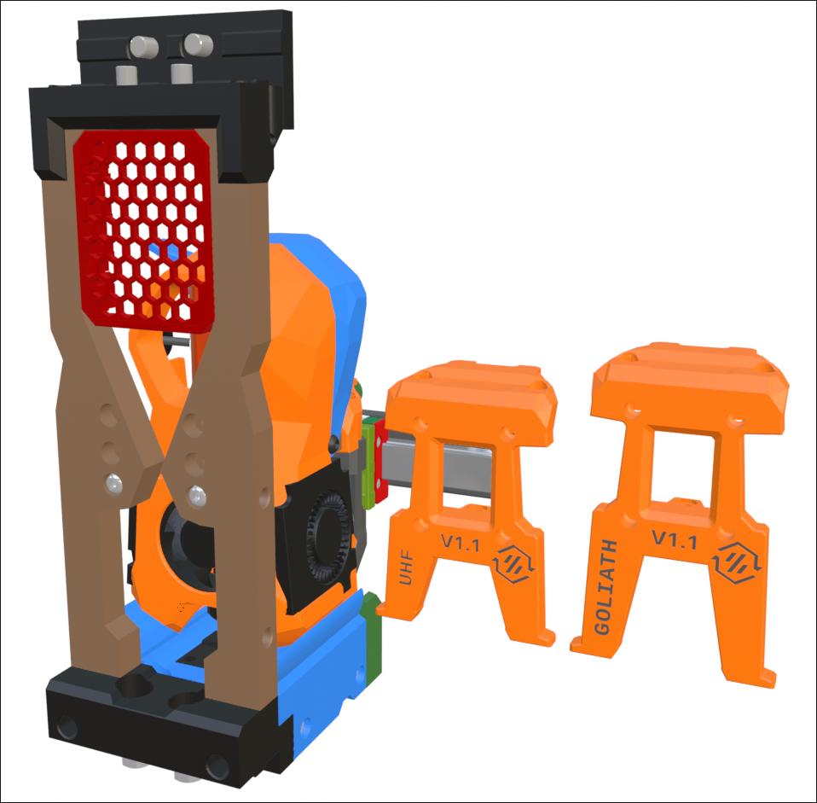
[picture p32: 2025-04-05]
Common_Parts/StealthChanger/ModularDock/ModularDock.png

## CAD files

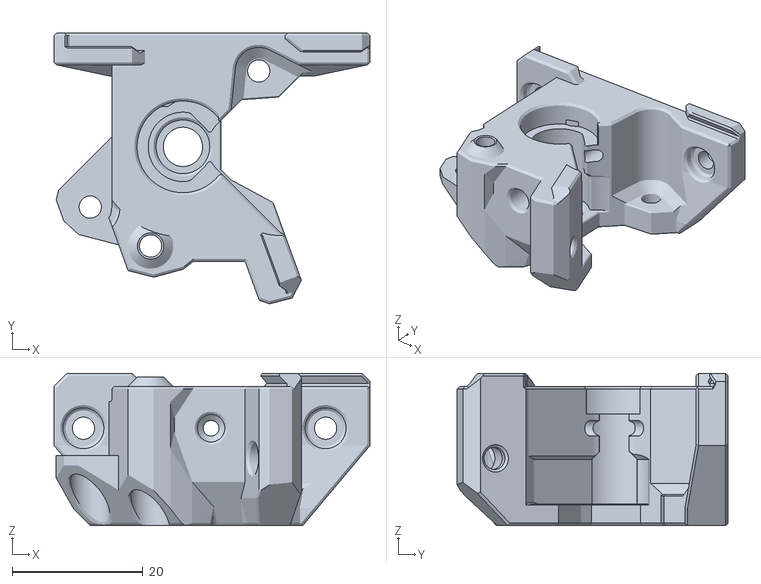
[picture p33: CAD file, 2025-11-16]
Filament_Cutter/WW_BMG_Main_Body_withCutter.stl
48.3 x 41.4 x 23.3

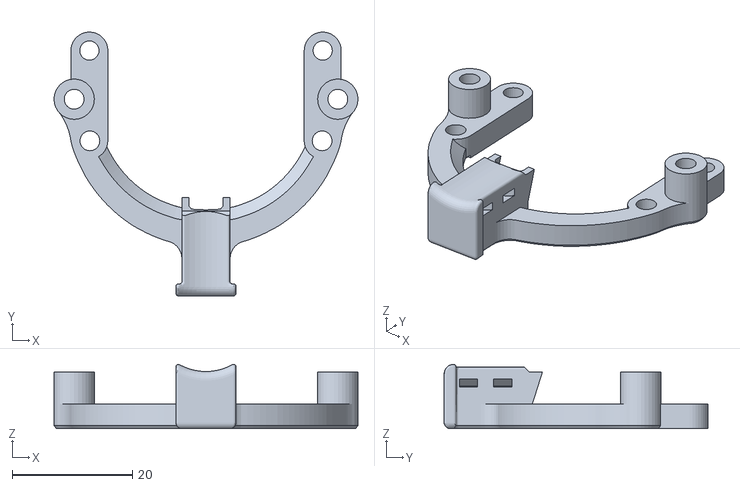
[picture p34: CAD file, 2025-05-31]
Common_Parts/4040_VSlot/4040_VSlot_Pcb_Mount.stl
50.6 x 43.9 x 10.7

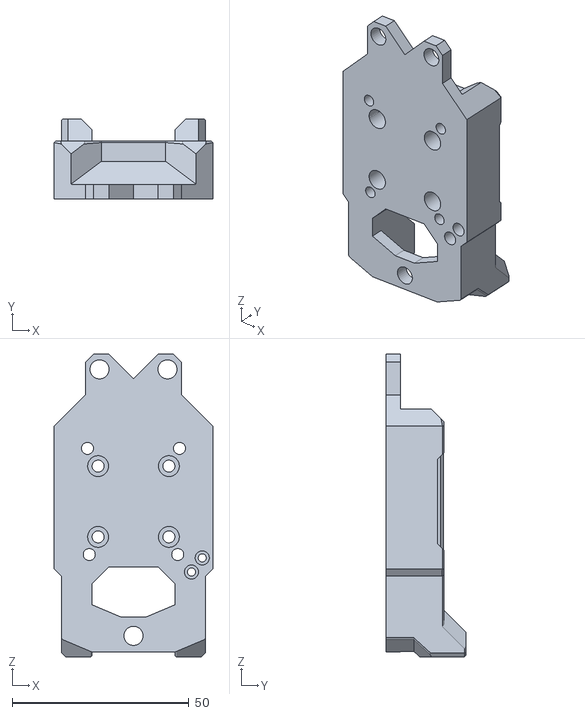
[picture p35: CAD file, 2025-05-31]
Common_Parts/4040_VSlot/UHF/4040_VSlot_Beacon3D_UHF.stl
44.8 x 22.5 x 85.6

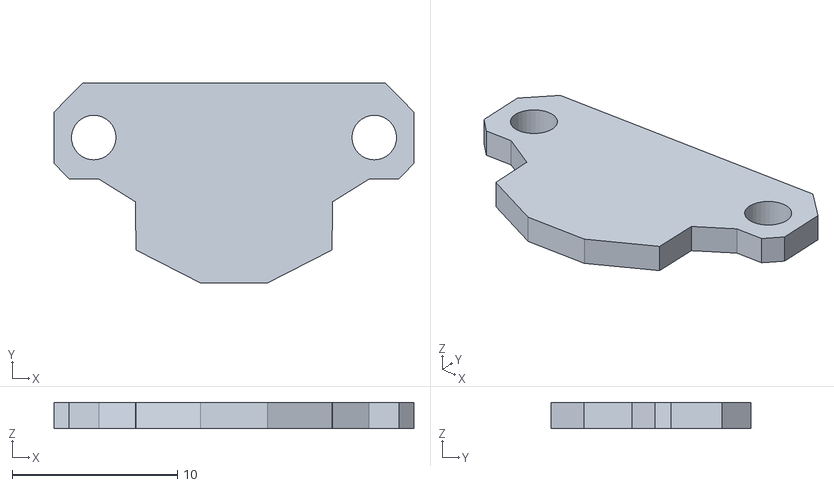
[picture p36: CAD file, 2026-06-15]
Common_Parts/Biqu MicroProbe v2 1.6mm Spacer.stl
21.8 x 12.1 x 1.60

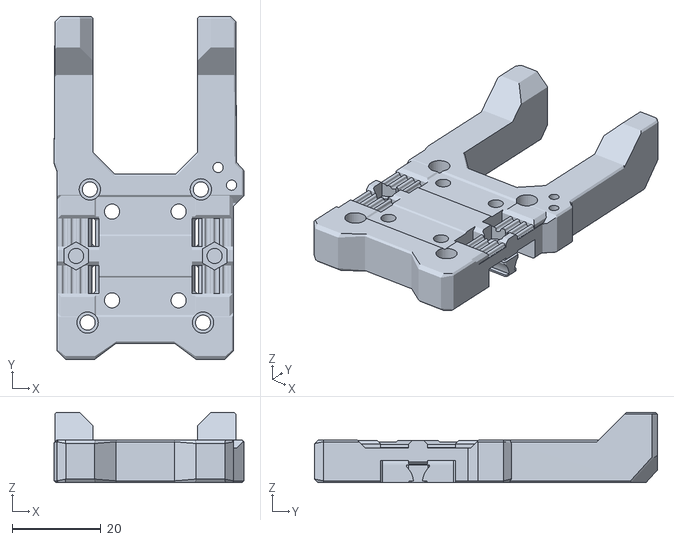
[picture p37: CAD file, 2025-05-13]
Common_Parts/MGN12C_Front_Rigid/Goliath/MGN12C_Front_Rigid_Goliath_Beacon.stl
42.7 x 77.3 x 15.8

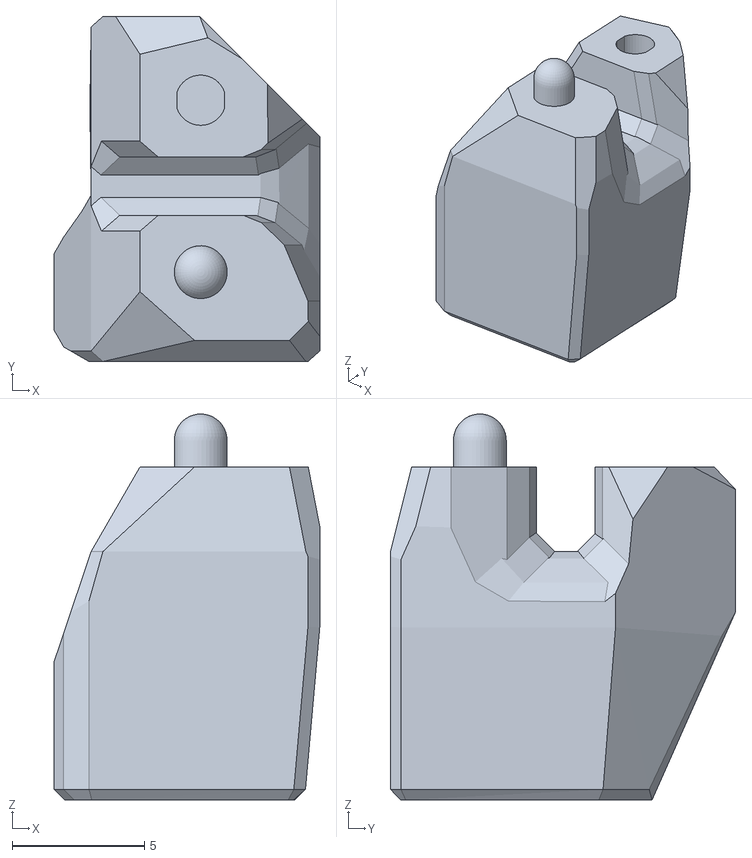
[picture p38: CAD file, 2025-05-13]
Common_Parts/MGN12C_Front_Rigid/MGN12C_Front_Rigid_X-Stop_Mount.stl
10.0 x 13.0 x 14.6

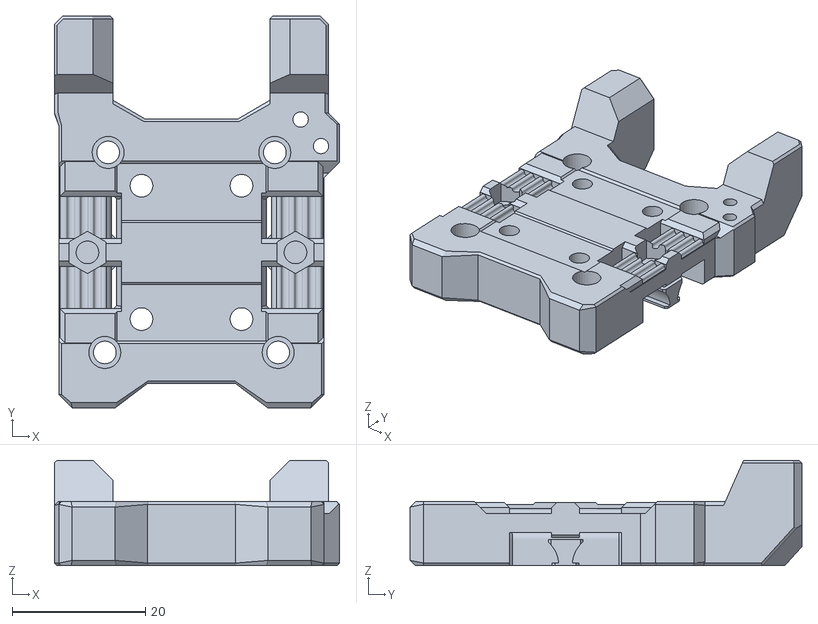
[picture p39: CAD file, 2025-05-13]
Common_Parts/MGN12C_Front_Rigid/Standard/MGN12C_Front_Rigid_Beacon.stl
42.7 x 58.8 x 15.8

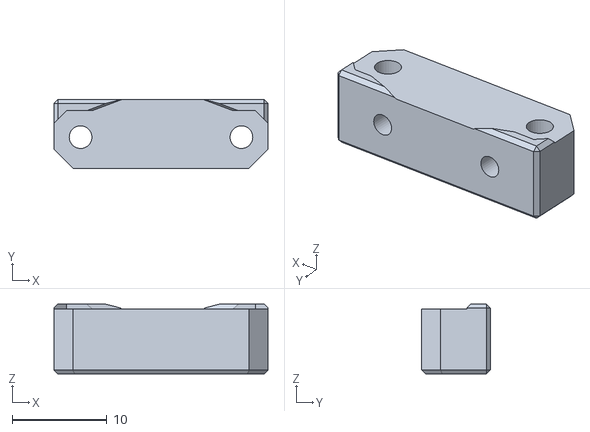
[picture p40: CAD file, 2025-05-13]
Common_Parts/MGN12C_Front_Rigid/UHF/MGN12C_Front_Rigid_UHF_MicroProbe_Mount.stl
22.6 x 7.26 x 7.36

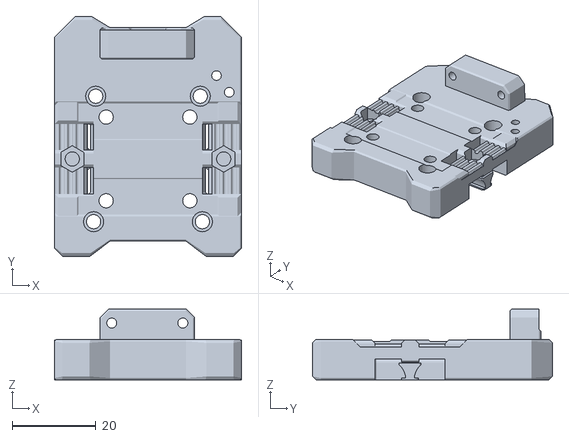
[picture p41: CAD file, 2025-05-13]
Common_Parts/MGN12H_Front_Rigid/Goliath/MGN12H_Front_Rigid_Goliath_MicroProbe.stl
44.8 x 57.4 x 16.9

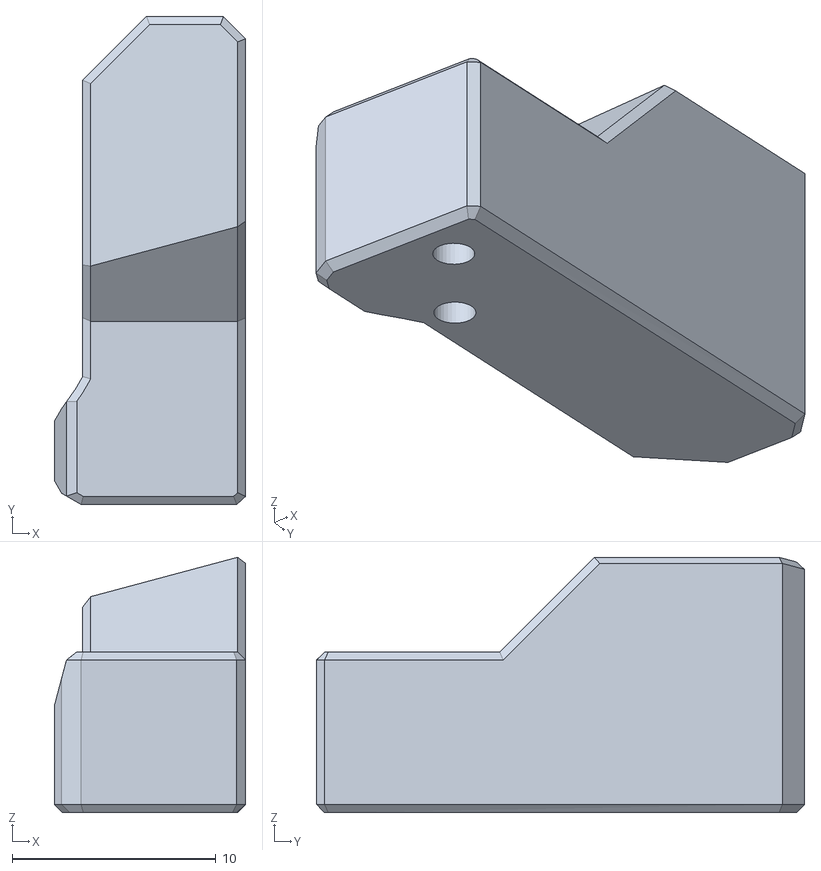
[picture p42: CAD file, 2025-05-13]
Common_Parts/MGN12H_Front_Rigid/MGN12H_Rigid_x-carriage_Gantry_X_stop_Boss.stl
9.40 x 24.0 x 12.5

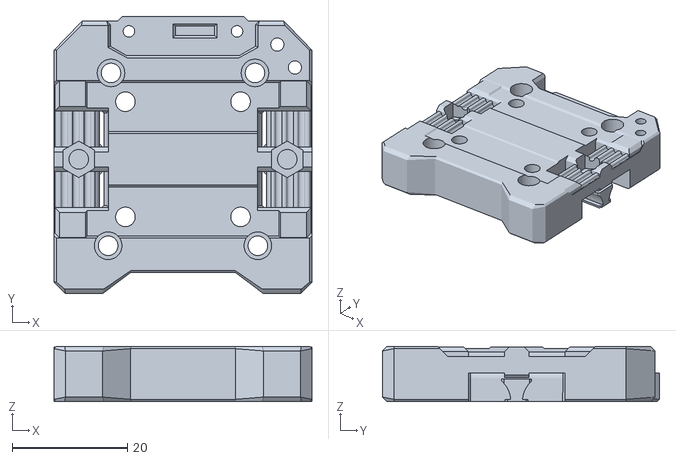
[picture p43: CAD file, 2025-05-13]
Common_Parts/MGN12H_Front_Rigid/Standard/MGN12H_Front_Rigid_Differential_IR.stl
44.8 x 48.1 x 9.60

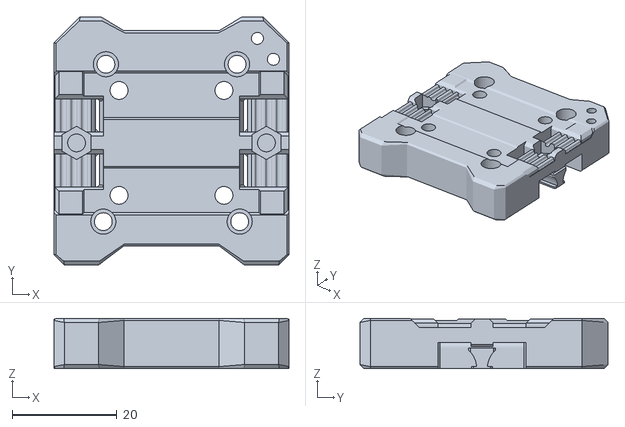
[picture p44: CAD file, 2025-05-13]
Common_Parts/MGN12H_Front_Rigid/UHF/MGN12H_Front_Rigid_no-probe.stl
44.8 x 47.4 x 9.60

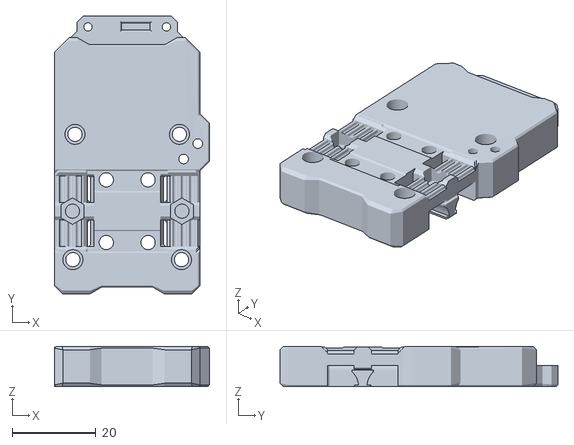
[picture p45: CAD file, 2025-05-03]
Common_Parts/MGN9C_Front_Rigid/Goliath/MGN9C_Front_Rigid_Goliath_DiffIR_Probe.stl
37.1 x 66.5 x 9.60

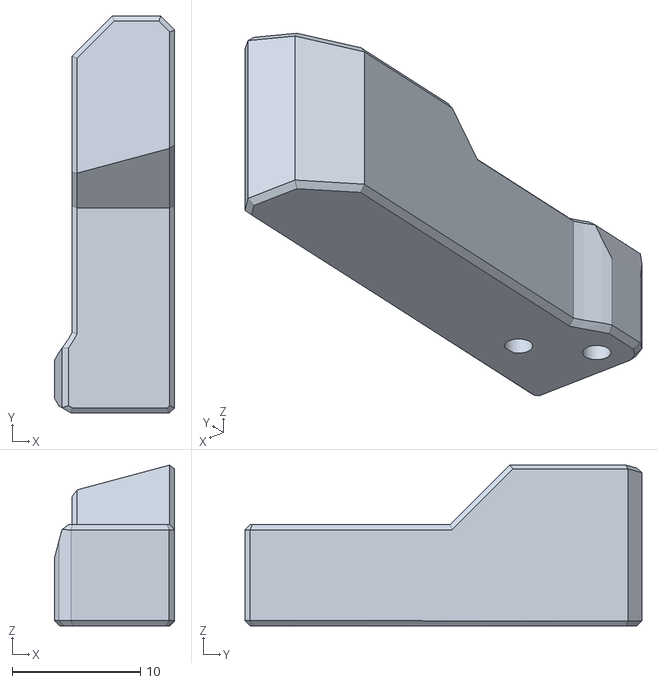
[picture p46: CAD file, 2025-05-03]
Common_Parts/MGN9C_Front_Rigid/MGN9C_Rigid_x-carriage_Gantry_X_stop_Boss.stl
9.40 x 31.0 x 12.5

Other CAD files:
Common_Parts/MGN9C_Front_Rigid/Standard/MGN9C_Front_Rigid_Beacon.stl
Common_Parts/MGN9C_Front_Rigid/UHF/MGN9C_Front_Rigid_UHF_DiffIR_Probe.stl
Common_Parts/MGN9H_Front_Rigid/Goliath/MGN9H_Front_Rigid_Goliath_MicroProbe.stl
Common_Parts/MGN9H_Front_Rigid/MGN9H_Front_Rigid_X-Stop_Mount.stl
Common_Parts/Blower_guide_gluing_tool_M3x20.stl
Common_Parts/Blower_guide_x2.stl
Common_Parts/Knomi2_Clip.stl
Common_Parts/MGN12C_Front_Rigid/Goliath/MGN12C_Front_Rigid_Goliath_BL-Touch.stl
Common_Parts/MGN12C_Front_Rigid/Goliath/MGN12C_Front_Rigid_Goliath_BTT_Eddy.stl
Common_Parts/MGN12C_Front_Rigid/Goliath/MGN12C_Front_Rigid_Goliath_Differential_IR.stl
Common_Parts/MGN12C_Front_Rigid/Goliath/MGN12C_Front_Rigid_Goliath_Euclid.stl
Common_Parts/MGN12C_Front_Rigid/Goliath/MGN12C_Front_Rigid_Goliath_MicroProbe.stl
Common_Parts/MGN12C_Front_Rigid/Goliath/MGN12C_Front_Rigid_Goliath_Omron.stl
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

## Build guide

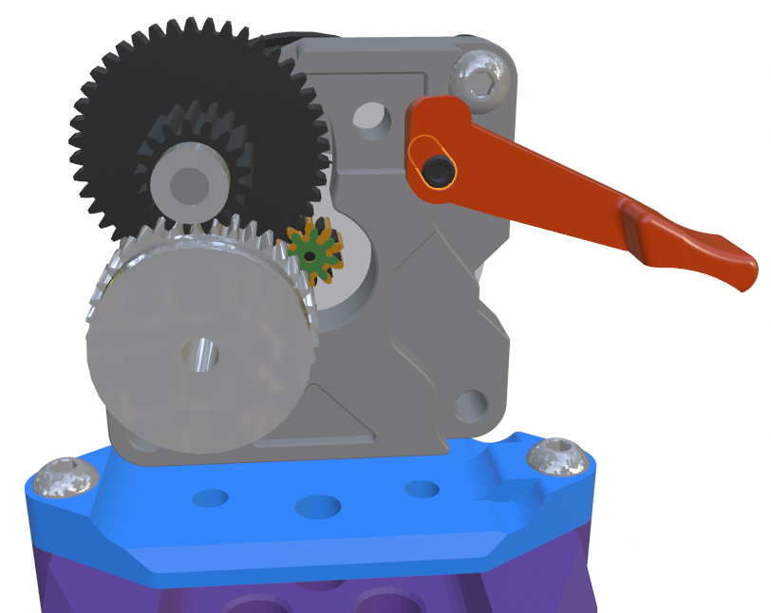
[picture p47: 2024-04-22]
Extruders/Hummingbird/Extruder_mods/Filament_release_lever_Install.png

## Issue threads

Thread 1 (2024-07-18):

Decorative cover for top hole

ADKMechETECH, 2024-07-18:
Maybe I missed it, but is there a decorative (or plain) cover for the top hole like there was for V1?

atrushing, 2024-07-18:
I have added the two versions in the *Common Parts* folder. The Sherpa extruders sit too close to the shroud so these hole covers will not fit with them unless using my VZ RIDGA version of the Sherpa Micro.

ADKMechETECH, 2024-07-18:
Awesome, thank you!

Closed 2024-07-18.

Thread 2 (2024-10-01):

x_carriage_frames_Beacon3D_MGN12.stl Mini Sherpa

chadakenn, 2024-10-01:
x_carriage_frames_Beacon3D_MGN12.stl for the Mini Sherpa and bltouch both parts dont sit level on the bed also any way to hit eddy in the middle

atrushing, 2024-10-01:
I probably need to double check all of the x-carriage pairs to see how many need to be fixed. For now, you could right click the x-frame .stl in the slicer and use the [Split] >> [To Objects] tool and the raised one should drop down to the build plate.
Thanks for letting me know about the issue.

chadakenn, 2024-10-01:
> I probably need to double check all of the x-carriage pairs to see how many need to be fixed. For now, you could right click the x-frame .stl in the slicer and use the [Split] >> [To Objects] tool and the raised one should drop down to the build plate. Thanks for letting me know about the issue.

i just dropped it down it was only one layer so hopfully itll still fit

atrushing, 2024-10-02:
Yeah, the one missing layer won't effect the geometry of the assembled x-carriage.

Closed 2024-10-01.

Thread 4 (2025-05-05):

MGN12H

Morrowshadow, 2025-05-05:
Hi, forgive me if this isn't how you ask questions, github is mighty confusing for me.

I plan on making this for the SV08, Likely using either a Sherpa Mini, or a WWG2, with a bambu hotend, using a BTT Eddy (Using EDDY-NG TAP)

Which carriage would I need?

Thank you for any help you can offer!

atrushing, 2025-05-13:
The new MGN12H rigid x-carriages are [in the repo](https://github.com/atrushing/Mini_Stealth/tree/main/Common_Parts/MGN12H_Front_Rigid) now.

Closed 2025-05-19.

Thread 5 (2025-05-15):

CAD file available?

Anacardium12, 2025-05-15:
Hi!
I would like to replace my current stock Mini Stealthburner with one with an Orbiter2.0 Extruder.
Extruder is already there.
The large number of options you provide is quite overwhelming.
Is there a CAD file or more detailed description of what is needed (to print, to buy and how to assemble)?
Best wishes

atrushing, 2025-05-15:
Yeah, this project seems to keep expanding..

I just updated the Orbiter [.blend file](https://github.com/atrushing/Mini_Stealth/blob/main/Extruders/Orbiter_2.0/Orbiter_2.0_Dragon_UHF_Example.blend) to include most of the key parts needed to build the Mini Stealth. This is the closest thing that I have to 'CAD' for this project. My working Blender file is almost 500 MB and I don't think it would be very helpful even if I could include it in the repo.

The parts shopping list is pretty short.

- 2x - 4010 blower - 24v
- 1x - 3010 fan - 24v
- 4x - 3x6mm magnets (I ran a toolhead without them for a good while but they do make the connection stronger)
- 3x - NeoPixel RGBW LEDs
    - or [Starlight](https://xrbunker.works/products/starlight-by-timmit) LEDs
- M3x4x5mm Voron standard heatset inserts
- Misc M3 button head cap screws

The print settings are Voron standard, ABS with 40% infill. The are about ten different parts that need to be printed.

- The core piece (based on extruder and hotend)
- The shroud (standard, UHF or Goliath)
- LED diffuser (white ABS or clear PETG)
- LED carrier (white ABS or clear PETG)
- 2x - Blower air guide + 1x install tool
- Cable door
- Motor bridge (to secure cable door and/or umbilical PCB and to provide cable management)

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

I designed a filament release [lever](https://github.com/atrushing/Mini_Stealth/blob/main/Extruders/Orbiter_2.0/Orbiter2.0_Filament_release_lever.stl) for the Orbiter 2.0 that requires a modified [idler arm](https://github.com/atrushing/Mini_Stealth/blob/main/Extruders/Orbiter_2.0/Orbiter2.0_Idler_arm_short.stl). There is more information about it in the Orbiter 2.0 readme.

The Mini Stealth might be able to fit on the aftermarket aluminum x-carriages for V0 printers. The weakest part of mounting the toolhead to the gantry was the stock x-carriage so I developed more rigid printed x-carriages for the V0.1 and the V0.2 printers. They are wider than stock because they have angled ribs that wrap around the side of the MGN7 or MGN9 linear carriage. This requires changing the XY_Joint_Upper_Left/Right pieces with the ones [here](https://github.com/atrushing/Mini_Stealth/tree/main/Common_Parts/V0_x-carriages).

Over on TeamFDM.com I have [a post](https://www.teamfdm.com/forums/topic/3433-mini-stealth-v2-is-available/?do=findComment&comment=25525&_rid=1756) that details all of the heatset insert locations. [Another post](https://www.teamfdm.com/forums/topic/1886-vorpal-180-a-printed-printer/?do=findComment&comment=13566&_rid=1756) there details the advantage of the air guides that I have added to the 4010 blowers. And finally, [this post](https://www.teamfdm.com/forums/topic/3433-mini-stealth-v2-is-available/?do=findComment&comment=19668&_rid=1756) explains how to install them.

[Assembly](https://www.teamfdm.com/forums/topic/1886-vorpal-180-a-printed-printer/?do=findComment&comment=15428&_rid=1756) is rather straightforward but I would suggest doing a test assembly before mounting the toolhead on your printer. This is mainly to verify screw lengths because I have crushed an MGN9 linear carriage because the main mounting screws were 0.5mm too long. A few M3 shim washers (DIN988) were able to solve the collision after I had to spring for a new linear rail/carriage set.

I think I will add this reply, but expand the linked information, into the main readme file but I am afraid that it will turn into a book before I'm done...

Good luck and happy printing!

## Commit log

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2024-04-22 Ender 3 and Hummingbird extruder readme files
    [Side_Mount_V0_CR-Touch_bracket_v0.2.stl]
2024-07-06 Added mounting options for Ender printers
    [1mm_thick_MGN9H_Spacer.stl, Belt Clamping Wedge.stl, Ender3_MGN12H_Front_x-frame_Left.stl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]
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2024-07-18 Add a filament release lever for the Sherpa Mini extruder
    [Filament_Release_Lever_Sherpa_Mini.stl, Housing_Core_ATR.stl, Idler_Arm_ATR.stl]
2024-07-18 Add cover options for the top hole of the shroud
    [Top_Hole_Cover_Decorative.stl, Top_Hole_Cover_Plain.stl]
2024-07-19 Fixed Top_Hole_Cover_Decorative.stl
    [Top_Hole_Cover_Decorative.stl]
2024-08-05 Added hex patterns for Crop-Top shrouds
    [Mini_Stealth_Crop-Top_Hex_Pattern.stl, Mini_Stealth_Crop-Top_UHF_Hex_Pattern.stl]
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2024-08-06 Fixed thin wall in shrouds below 4010 blowers
    All shroud files are new. This change mostly helps when printing with larger nozzles.
    https://www.teamfdm.com/uploads/monthly_2024_07/hole.PNG.4e27093753c6028b1fcccc07cb9f063c.PNG
    [[a]_MiniStealth_Shroud_GalileoSA.stl, [a]_MiniStealth_Shroud_GalileoSA_CropTop.stl, [a]_MiniStealth_Shroud_GalileoSA_CropTop_UHF.stl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]
2024-08-09 Added new shrouds for right side mounted probes
    [[a]_MiniStealth_Shroud_GalileoSA_ProbeRight.stl, [a]_MiniStealth_Shroud_GalileoSA_ProbeRight_CropTop.stl, [a]_MiniStealth_Shroud_GalileoSA_ProbeRight_CropTop_U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]
2024-08-09 Updated MGN12 mounts for Ender 3 printers
    These new MGN12 x-carriages are compatible with MGN12C and MGN12H linear carriages
    [Ender3_MGN12H_Front_x-frame_Left.stl, Ender3_MGN12H_Front_x-frame_Left_v1.1.stl, Ender3_MGN12H_Front_x-frame_Right.stl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]
2024-08-12 Added Beacon mounts for Ender 3 x-carriages
    [Ender3_MGN12_Front_x-frame_Beacon.stl, Ender3_MGN9H_Front_x-frame_Beacon.stl]
2024-08-13 added temp configurator working files
    [Mini_Stealth_Sherpa_Micro_configurations.xlsx]
2024-08-14 Added Ender 3 mounts for Biqu MicroProbe
    [Ender3_MGN12_Front_x-frame_MicroProbe.stl, Ender3_MGN9H_Front_x-frame_MicroProbe.stl]
2024-08-14 Added shroud for Goliath hotend
    [[a]_MiniStealth_Shroud_Goliath_CropTop.stl]
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2025-02-09 Mesh cleanup, added new extruders and readme improvements
    Added support for WristWatch BMG & G2SA extruders
    There are now two versions for the Sherpa Micro, normal and mirrored. (the mirrored version fits my modification with a filament release lever on the left side)
    Added the modded+mirrored Sherpa Micro .stl files in this repo
    Added support for HGX Lite extruder
    Added support for Creality K1 extruder
    Added support for Goliath hotend (CropTop only)
    Added 2.4/Trident x-frames for Goliath hotend
    Minor shroud geometry cleanup
    Fixed mis-aligned first layer of x-frame pieces
    Added support for 2510 hotend fan to all shroud options
    Added right side probe support
    Added new hex patterns to fit the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
    [Alternate_Orbiter1.5_Filament_release_lever.stl, Alternate_Orbiter1.5_Idler_arm_short.stl, CrealityK1_CableChain_2hole_mount.stl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]
2025-03-16 Adding new style of Core pieces
    [MiniStealth_Core_SherpaMini_Alt_Bambu.stl, MiniStealth_Core_SherpaMini_Alt_Dragon.stl, MiniStealth_Core_SherpaMini_Alt_DragonACE.stl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]
2025-03-26 Added Prusa MK3 x-carriage options
    [Prusa_x-carriage_Back_Plate.stl, Prusa_x-carriage_Front_Plate.stl, Prusa_x-carriage_Front_Plate_PINDA.stl]
2025-03-30 Added new style of core pieces for all extruders
    [MiniStealth_Core_LgxLite_Bambu_Rigid.stl, MiniStealth_Core_LgxLite_DragonACE_Rigid.stl, MiniStealth_Core_LgxLite_Dragon_Rigid.stl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]
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2025-04-05 Updated StealthChanger parts and dock
    [Back_Mini_Stealth.stl, Base_Mini_Stealth.stl, Cup_Body_Mini_Stealth.stl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]
2025-04-24 Update to DAB design and readme
    [DAB_Mini_Stealth_v0.8.stl, DAB_Stealthburner.stl, DAB_Stealthburner_Switchwire_back.stl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]
2025-05-03 Added rigid x-carriages for MGN9C and MGN9H linear rails
    [DAB_Stealthburner_Z_Stop_boss.stl, DAB_Stealthburner_Z_Stop_boss_GantryPod_X_Stop.stl, DAB_Stealthburner_Z_Stop_boss_X_Stop.stl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]
2025-05-13 Added new x-carriages for MGN12C/H linear rails
    [MGN12C_Front_Rigid_Beacon.stl, MGN12C_Front_Rigid_Differential_IR.stl, MGN12C_Front_Rigid_Euclid.stl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]
2025-05-22 Added new cores for E3D V6 compatible hotends
    [MiniStealth_Core_LgxLite_V6.stl, MiniStealth_Core_LgxLite_V6_Rigid.stl, MiniStealth_Core_Orb1.5_V6.stl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]
2025-05-30 Add 4040 VSlot support
    [4040_VSlot_Beacon3D_UHF.stl, 4040_VSlot_Pcb_Mount.stl]
2025-09-03 Added x-frames for Voron Legacy printers
    [Belt_Clamp_x2.stl, x-Frame_Mini_Stealth_left.stl, x-Frame_Mini_Stealth_right.stl]
2025-09-25 Added BTT Eddy side-mount variants
    [Side_Mount_V0_BTT_Eddy_bracket_1.5mm_Lower.stl, Side_Mount_V0_BTT_Eddy_bracket_1mm_Lower.stl]
2025-10-26 Added x-carriage to fit the Tiny-M printer
    [bw_dd_sch_toolhead_MiniStealth_left.stl, bw_dd_sch_toolhead_MiniStealth_right.stl]
2025-11-16 Added WW BMG remix with Filament Cutter
    [Cutter_Arm.stl, Cutter_Arm_Subtract_Body.stl, WW_BMG_Backplate_withCutter.stl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]
2025-12-19 Minor geometry improvement for WW-BMG shrouds
    [[a]_MiniStealth_Shroud_WWBMG.stl, [a]_MiniStealth_Shroud_WWBMG_2510.stl, [a]_MiniStealth_Shroud_WWBMG_Knomi1.stl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]
2025-12-20 Added WristWatch Orbiter 2.x extruder and Mini Stealth shrouds for it
    [Bambu Filament Cutter_WW_Orb2.x.stl, Cutter_Arm_Subtract_Body_WWORB2.stl, MiniStealth_Core_Orb2.0_Bambu.stl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]
2025-12-24 Added cores for the Creality K1 hotend
    [MiniStealth_Core_LgxLite_Creality_K1.stl, MiniStealth_Core_LgxLite_Creality_K1_Rigid.stl, MiniStealth_Core_Orb1.5_Creality_K1.stl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]
2026-01-01 Added filament release lever to WWORB2x extruder
    [Filament_Release_Lever_WWORB2.stl, WWORB2_Rear_Body.stl, WWORB2_Rear_Body_FilCutter.stl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]
2026-02-12 Added XY_Joint_Upper pieces for Tulip Gantry
    [XY_Joint_Left_Upper_TulipMod_x1.stl, XY_Joint_Right_Upper_TulipMod_x1.stl]
2026-02-23 Added x-carriage for Sovol SV-06
    [x-carriage_SV06_back.stl, x-carriage_SV06_front.stl]
2026-03-06 Added PC4M6 and ECAS versions of Hummingbird mod
    [Front_Hex_grid_Hummingbird_ATR_ECAS.stl, Hummingbird_Front_ATR_ECAS.stl]
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2026-06-15 Added spacer for Biqu MicroProbe v2 and new Sovol SV06 x-carriage for UHF hotends
    [Biqu MicroProbe v2 1.6mm Spacer.stl, x-carriage_SV06_front_UHF.stl]
